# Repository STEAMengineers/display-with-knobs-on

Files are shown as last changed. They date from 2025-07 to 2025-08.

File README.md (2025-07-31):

# display-with-knobs-on

Think [cheap yellow display](https://github.com/witnessmenow/ESP32-Cheap-Yellow-Display) but not necessarily yellow and with two joystick inputs and four channels of brushed motor output. Originally designed to control [The open source underwater vehicle](https://github.com/concretedog/Tiny-Opensource-Underwater-Vehicle-TOUV-) project. 

## Features

* [RP2350b](https://datasheets.raspberrypi.com/rp2350/rp2350-product-brief.pdf) - Dual Arm Cortex-M33 or dual Hazard3 RISC-V processors
@ 150MHz
* [W25Q128JV-DTR](https://www.winbond.com/resource-files/w25q128jv_dtr%20revc%2003272018%20plus.pdf) - 16Mb primary flash 
* [MSP3520 screen](https://www.lcdwiki.com/3.5inch_SPI_Module_ILI9488_SKU%3AMSP3520) - ILI9488 powered 320x480 LCD screen with resistive touch and SD card slot (Headers)
* 2 x [TB6612FNG](https://toshiba.semicon-storage.com/us/product/linear/motordriver/detail.TB6612FNG.html) - Four channels of brushed motor outputs
* [IP5310](https://www.injoinic.com/api//static/uploads/20250528/20250528180445_6836dfbd54166.pdf) - Battery charger management with 3A boost output @ 5V for motors
* 2 x Joystick - Two axis analoge joysticks with push button inputs

  ## GPIO

  ### Motors

  A
  * IN1 - GPIO29
  * IN2 - GPIO28
  * PWM - GPIO24

  B
  * IN1 - GPIO31
  * IN2 - GPIO32
  * PWM - GPIO25

  STANDBY - GPIO30

  C
  * IN1 - GPIO34
  * IN2 - GPIO33
  * PWM - GPIO26

  D
  * IN1 - GPIO36
  * IN2 - GPIO37
  * PWM - GPIO27

  STANDBY - GPIO35

  ### Joysticks
  A
  * X - GPIO43
  * Y - GPIO44
  * Button - GPIO39
 
  B
  * X - GPIO41
  * Y - GPIO42
  * Button - GPIO38
 
  ### Screen

  Display
  * CS - GPIO13
  * RESET - GPIO18
  * DC/RS - GPIO17
  * MOSI - GPIO11
  * MISO - GPIO12
  * SCK - GPIO14
  * LED - GPIO16
 
  Touch
  * CS - GPIO10
  * IRQ - GPIO15
  * MOSI - GPIO11
  * MISO - GPIO12
  * SCK - GPIO14
 
  SD card
  * CS - GPIO21
  * SCK - GPIO22
  * MOSI - GPIO19
  * MISO - GPIO20

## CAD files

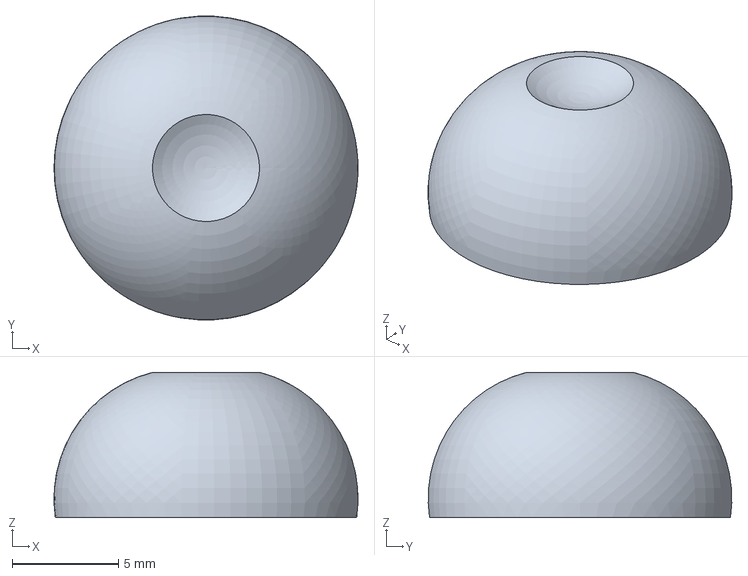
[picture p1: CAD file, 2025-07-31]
freecad/joystick_mushroom2.FCStd
14.3 x 14.3 x 6.82 mm

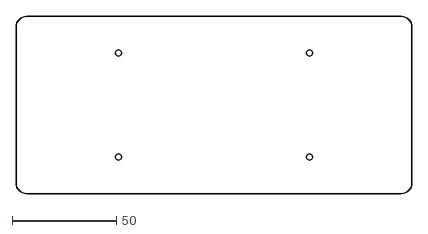
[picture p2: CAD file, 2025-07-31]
kicad/display-with-knobs-on/edgecuts.dxf
190.0 x 85.0

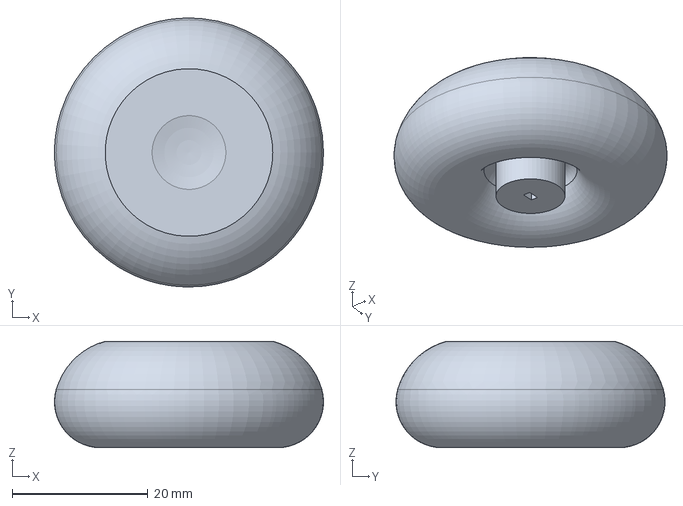
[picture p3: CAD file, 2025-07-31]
freecad/joystick_mushroom.FCStd
39.6 x 39.6 x 15.7 mm

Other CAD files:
freecad/joystick_mushroom.stl
freecad/joystick_mushroom2.stl

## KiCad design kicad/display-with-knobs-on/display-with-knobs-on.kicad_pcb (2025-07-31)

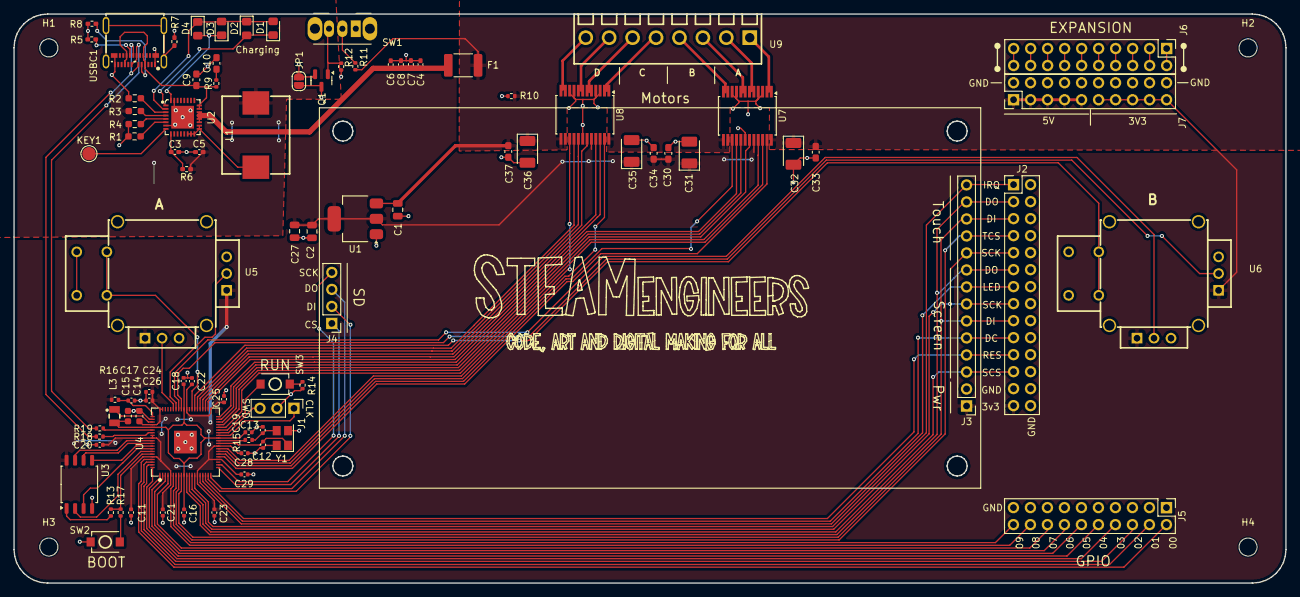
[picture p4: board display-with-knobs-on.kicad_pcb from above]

Board: 2 copper layers, 190.0 x 85.0 mm, 92 parts (1 on the bottom side), 106 nets.

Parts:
C1, C2, C27: 10u; C_0805_2012Metric
C3, C4, C5, C6, C7, C8: 22uF; C_0402_1005Metric_Pad0.74x0.62mm_HandSolder
C9, C10: 10uF; C_0603_1608Metric_Pad1.08x0.95mm_HandSolder
C11, C16, C19, C20, C21, C22, C23, C24, C25, C26, C28, C29: 100n; C_0402_1005Metric
C12, C13: 15p; C_0402_1005Metric
C14, C15: 4.7u; C_0603_1608Metric
C17, C18: 4.7u; C_0402_1005Metric
C30, C33, C34, C37: 0.1uF; C_0603_1608Metric_Pad1.08x0.95mm_HandSolder
C31, C32, C35, C36: 10uF; CP_EIA-3528-21_Kemet-B_Pad1.50x2.35mm_HandSolder
CN1: S2B-PH-SM4-TB(LF)(SN); CONN-SMD_P2.00_S2B-PH-SM4-TB-LF-SN
D1, D2, D3, D4: LED; LED_0805_2012Metric_Pad1.15x1.40mm_HandSolder
F1: Polyfuse; Fuse_1812_4532Metric_Pad1.30x3.40mm_HandSolder
H1, H2, H3, H4: MountingHole; MountingHole_2.7mm_M2.5
J1: Conn_01x03_Pin; PinHeader_1x03_P2.54mm_Vertical
J2: Conn_02x14_Odd_Even; PinHeader_2x14_P2.54mm_Vertical
J3: Conn_01x14_Socket; PinHeader_1x14_P2.54mm_Vertical
J4: Conn_01x04_Socket; PinHeader_1x04_P2.54mm_Vertical
J5, J6, J7: Conn_02x10_Odd_Even; PinHeader_2x10_P2.54mm_Vertical
JP1: Jumper_on; SolderJumper-2_P1.3mm_Open_RoundedPad1.0x1.5mm
KEY1: TestPoint; TestPoint_Pad_D2.0mm
L1: MHCC10040-1R0M-R7; IND-SMD_L11.6-W10.1
L3: 3.3u; IND-SMD_L2.0-W1.6_AOTA-B201610S3R3-101-T
Q1: JSM2302; SOT-23
R1: 51K; R_0603_1608Metric_Pad0.98x0.95mm_HandSolder
R2, R3, R4: 0; R_0603_1608Metric_Pad0.98x0.95mm_HandSolder
R5, R8: 5.1K; R_0402_1005Metric_Pad0.72x0.64mm_HandSolder
R6: 0; R_0402_1005Metric_Pad0.72x0.64mm_HandSolder
R7: 1M; R_0402_1005Metric_Pad0.72x0.64mm_HandSolder
R9: 2R; R_0402_1005Metric
R10: R120; R_0402_1005Metric
R11: 10K; R_0402_1005Metric
R12: 100K; R_0402_1005Metric
R13: 0; R_0402_1005Metric
R14, R15, R17: 1k; R_0402_1005Metric
R16: 33; R_0402_1005Metric
R18, R19: 27; R_0402_1005Metric
SW1: ON/OFF; SW_Slide_SPDT_Angled_CK_OS102011MA1Q
SW2, SW3: SW_Push; SW-SMD_L3.9-W3.0-P4.45
U1: NCP1117-3.3_SOT223; SOT-223-3_TabPin2
U2: IP5310; QFN-32_L5.0-W5.0-P0.50-BL-EP3.4
U3: W25Q128JVS; SOIC-8_5.23x5.23mm_P1.27mm
U4: RP2350_80QFN; QFN-80_L10.0-W10.0-P0.40-TL-EP3.4
U5, U6: YF16S-FL7.2-B5KB(45-10)-Y; JOYTICK-TH_YF16S-FL7.2-B5KB-45-10-Y_1
U7, U8: TB6612FNG; SSOP-24_5.3x8.2mm_P0.65mm
U9: DB125-3.5-8P-GN-S; CONN-TH_8P-P3.50_DORABO_DB125-3.5-8P-GN-S
USBC1: 105450-0101; USB-C-SMD_TYPE-C-USB-18
Y1: ABM8-272-T3; Crystal_SMD_3225-4Pin_3.2x2.5mm

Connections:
+1V1: C15.1, C16.1, C18.1, C19.1, L3.1, U4.10 (DVDD), U4.32 (DVDD), U4.51 (DVDD), U4.65 (VREG_FB)
+3V3: C2.1, C11.1, C14.1, C20.1, C21.1, C22.1, C23.1, C24.1, C25.1, C26.1, C27.1, C28.1, C29.1, C30.1, C31.1, C34.1, C35.1, J2.27, J3.1, J7.11, J7.13, J7.15, J7.17, J7.19, R16.1, U1.2 (VO), U3.8 (VCC), U4.5 (IOVDD), U4.15 (IOVDD), U4.24 (IOVDD), U4.29 (IOVDD), U4.41 (IOVDD), U4.50 (IOVDD), U4.59 (ADC_AVDD), U4.60 (IOVDD), U4.64 (VREG_VIN), U4.68 (USB_OTP_VDD), U4.69 (QSPI_IOVDD), U4.76 (IOVDD), U5.1, U5.4, U6.1, U6.4, U7.20 (VCC), U8.20 (VCC)
+5V: C1.1, C32.1, C33.1, C36.1, C37.1, F1.1, J7.1, J7.3, J7.5, J7.7, J7.9, R10.2, R11.1, U1.3 (VI), U7.13 (VM2), U7.14 (VM3), U7.24 (VM1), U8.13 (VM2), U8.14 (VM3), U8.24 (VM1)
+BATT: C5.1, CN1.2, L1.2, R3.1, R6.1
-BATT: C3.2, C4.2, C5.2, C6.2, C7.2, C8.2, C9.2, C10.2, CN1.1, JP1.1, Q1.2 (S), R1.1, R2.1, R4.1, R5.2, R7.2, R8.2, R12.2, U2.7 (AGND), U2.31 (LIGHT), U2.33 (EP), USBC1.A1 (GND), USBC1.A12 (GND), USBC1.B1 (GND), USBC1.B12 (GND)
/Controller/FLASH_SS: R13.2, U3.1 (~CS)
/Controller/QSPI_SCLK: U3.6 (CLK), U4.71 (QSPI_SCLK)
/Controller/QSPI_SD0: U3.5 (DI(IO0)), U4.72 (QSPI_SD0)
/Controller/QSPI_SD1: U3.2 (DO(IO1)), U4.74 (QSPI_SD1)
/Controller/QSPI_SD2: U3.3 (IO2), U4.73 (QSPI_SD2)
/Controller/QSPI_SD3: U3.7 (IO3), U4.70 (QSPI_SD3)
/Controller/QSPI_SS: R13.1, R17.1, U4.75 (QSPI_SS)
/Controller/RUN: SW3.2, U4.35 (RUN)
/Controller/VREG_AVDD: C17.1, R16.2, U4.61 (VREG_AVDD)
/Controller/VREG_LX: L3.2, U4.63 (VREG_LX)
/Controller/XIN: C12.1, U4.30 (XIN), Y1.1
/Controller/XOUT: R15.1, U4.31 (XOUT)
/Controller/~USB_BOOT: R17.2, SW2.2
/Power/VBUS: C9.1, R9.1, U2.23 (VIN), U2.24 (VIN), USBC1.A4 (VBUS), USBC1.A9 (VBUS), USBC1.B4 (VBUS), USBC1.B9 (VBUS)
A1: U7.1 (AO1), U7.2 (AO1), U9.1
A2: U7.5 (AO2), U7.6 (AO2), U9.2
ABUTTON: U4.48 (GPIO39), U5.8
AIN1: U4.37 (GPIO29), U7.21 (AIN1)
AIN2: U4.36 (GPIO28), U7.22 (AIN2)
AX: U4.54 (GPIO43_ADC3), U5.5
AY: U4.55 (GPIO44_ADC4), U5.2
B1: U7.11 (BO1), U7.12 (BO1), U9.4
B2: U7.7 (BO2), U7.8 (BO2), U9.3
BBUTTON: U4.47 (GPIO38), U6.8
BIN1: U4.39 (GPIO31), U7.17 (BIN1)
BIN2: U4.40 (GPIO32), U7.16 (BIN2)
BX: U4.52 (GPIO41_ADC1), U6.5
BY: U4.53 (GPIO42_ADC2), U6.2
C1: U8.1 (AO1), U8.2 (AO1), U9.5
C2: U8.5 (AO2), U8.6 (AO2), U9.6
CC1: R8.1, USBC1.A5 (CC1)
CC2: R5.1, USBC1.B5 (CC2)
CIN1: U4.43 (GPIO34), U8.21 (AIN1)
CIN2: U4.42 (GPIO33), U8.22 (AIN2)
D1: U8.11 (BO1), U8.12 (BO1), U9.8
D2: U8.7 (BO2), U8.8 (BO2), U9.7
D+: R18.1, USBC1.A6 (D+), USBC1.B6 (D+)
D-: R19.1, USBC1.A7 (D-), USBC1.B7 (D-)
DIN1: U4.45 (GPIO36), U8.17 (BIN1)
DIN2: U4.46 (GPIO37), U8.16 (BIN2)
GND: C1.2, C2.2, C11.2, C12.2, C13.2, C14.2, C15.2, C16.2, C17.2, C18.2, C19.2, C20.2, C21.2, C22.2, C23.2, C24.2, C25.2, C26.2, C27.2, C28.2, C29.2, C30.2, C31.2, C32.2, C33.2, C34.2, C35.2, C36.2, C37.2, J1.2, J2.2, J2.4, J2.6, J2.8, J2.10, J2.12, J2.14, J2.16, J2.18, J2.20, J2.22, J2.24, J2.25, J2.26, J2.28, J3.2, J5.1, J5.3, J5.5, J5.7, J5.9, J5.11, J5.13, J5.15, J5.17, J5.19, J7.2, J7.4, J7.6, J7.8, J7.10, J7.12, J7.14, J7.16, J7.18, J7.20, JP1.2, Q1.3 (D), R10.1, R14.2, SW2.1, U1.1 (GND), U3.4 (GND), U4.62 (VREG_PGND), U4.81 (GND), U5.3, U5.6, U5.7, U6.3, U6.6, U6.7, U7.3 (PGND1), U7.4 (PGND1), U7.9 (PGND2), U7.10 (PGND2), U7.18 (GND), U8.3 (PGND1), U8.4 (PGND1), U8.9 (PGND2), U8.10 (PGND2), U8.18 (GND), Y1.2, Y1.4
GPIO_0: J5.2, U4.77 (GPIO0)
GPIO_1: J5.4, U4.78 (GPIO1)
GPIO_2: J5.6, U4.79 (GPIO2)
GPIO_3: J5.8, U4.80 (GPIO3)
GPIO_4: J5.10, U4.1 (GPIO4)
GPIO_5: J5.12, U4.2 (GPIO5)
GPIO_6: J5.14, U4.3 (GPIO6)
GPIO_7: J5.16, U4.4 (GPIO7)
GPIO_8: J5.18, U4.6 (GPIO8)
GPIO_9: J5.20, U4.7 (GPIO9)
unnamed: C4.1, C6.1, C7.1, C8.1, F1.2, U2.19 (VOUT), U2.20 (VOUT), U2.21 (VOUT), U2.22 (VOUT)
unnamed: C10.1, R9.2
unnamed: C13.1, R15.2, Y1.3
unnamed: D1.2 (A), D2.1 (K), D3.2 (A), D4.1 (K), U2.2 (L3)
unnamed: D1.1 (K), D2.2 (A), U2.1 (L2)
unnamed: D3.1 (K), D4.2 (A), U2.32 (L1)
unnamed: J6.1, J6.2
unnamed: J6.3, J6.4
unnamed: J6.5, J6.6
unnamed: J6.7, J6.8
unnamed: J6.9, J6.10
unnamed: J6.11, J6.12
unnamed: J6.13, J6.14
unnamed: J6.15, J6.16
unnamed: J6.17, J6.18
unnamed: J6.19, J6.20
unnamed: L1.1, U2.14 (LX), U2.15 (LX), U2.16 (LX), U2.17 (LX), U2.18 (LX)
unnamed: Q1.1 (G), R12.1, SW1.3 (C)
unnamed: R14.1, SW3.1
unnamed: R11.2, SW1.2 (B)
unnamed: C3.1, R6.2, U2.9 (BAT)
unnamed: KEY1.1, U2.8 (KEY)
unnamed: R1.2, U2.6 (NTC)
unnamed: R4.2, U2.5 (RSET)
unnamed: R2.2, U2.3 (VSET)
unnamed: R3.2, U2.4 (VTHS)
unnamed: R19.2, U4.66 (USB_DM)
unnamed: R18.2, U4.67 (USB_DP)
unnamed: R7.1, USBC1.0
PWMA: U4.25 (GPIO24), U7.23 (PWMA)
PWMB: U4.26 (GPIO25), U7.15 (PWMB)
PWMC: U4.27 (GPIO26), U8.23 (PWMA)
PWMD: U4.28 (GPIO27), U8.15 (PWMB)
SC_CS: J2.23, J3.3, U4.12 (GPIO13)
SC_DC_RS: J2.19, J3.5, U4.17 (GPIO17)
SC_LED: J2.13, J3.8, U4.16 (GPIO16)
SC_RESET: J2.21, J3.4, U4.18 (GPIO18)
SC_SCK: J2.9, J2.15, J3.7, J3.10, U4.13 (GPIO14)
SC_SDI_MOSI: J2.5, J2.17, J3.6, J3.12, U4.9 (GPIO11)
SC_SDO_MISO: J2.3, J2.11, J3.9, J3.13, U4.11 (GPIO12)
SC_TS_CS: J2.7, J3.11, U4.8 (GPIO10)
SC_TS_IRQ: J2.1, J3.14, U4.14 (GPIO15)
SD_CS: J4.1, U4.21 (GPIO21)
SD_MISO: J4.3, U4.20 (GPIO20)
SD_MOSI: J4.2, U4.19 (GPIO19)
SD_SCK: J4.4, U4.22 (GPIO22)
STBY_A: U4.38 (GPIO30), U7.19 (STBY)
STBY_B: U4.44 (GPIO35), U8.19 (STBY)
SWCLK: J1.1, U4.33 (SWCLK)
SWD: J1.3, U4.34 (SWD)

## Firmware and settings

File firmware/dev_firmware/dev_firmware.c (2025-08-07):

#include <stdio.h>
#include "pico/stdlib.h"
#include "hardware/spi.h"
#include "hardware/adc.h"
#include "hardware/pwm.h"
#include "math.h"
#include "lib/screen.h"
#include "lvgl/lvgl.h"
#include "lib/anim_frames.h"
#include "motors.h"
#include "pins.h"

//#include "lib/ili9488.h"

//TODO -SCREEN

//Improve GUI
//  -Add image to controls
//  -Add animation picture frame


#define DISPLAY_WIDTH 480
#define DISPLAY_HEIGHT 320
// Buffer for the display
#define LV_COLOR_SIZE 2

static uint8_t buf1[DISPLAY_WIDTH * 320 * LV_COLOR_SIZE];


//float deadzone = 0.05f; // Deadzone for motor control
// Global variable to store the last speed of motor A
lv_obj_t * bar_motor_a = NULL;
// Global variable to store the last speed of motor B
lv_obj_t * bar_motor_b = NULL;

lv_obj_t *scale = NULL;
lv_obj_t *dial_label = NULL;
static lv_obj_t * dive_dial = NULL;

// Animation frames for the animation
const lv_image_dsc_t * anim_frames[] = {
    &animation00, &animation01, &animation02, &animation03, &animation04, &animation05, &animation06, &animation07,
    &animation08, &animation09, &animation10, &animation11, &animation12, &animation13, &animation14, &animation15,
    &animation16, &animation17, &animation18, &animation19, &animation20, &animation21, &animation22, &animation23,
    &animation24, &animation25, &animation26, &animation27, &animation28, &animation29, &animation30, &animation31,
    &animation32, &animation33, &animation34, &animation35, &animation36, &animation37
};

const uint8_t anim_frame_count = sizeof(anim_frames) / sizeof(anim_frames[0]);
static lv_obj_t * anim_img = NULL;
static uint8_t anim_frame_idx = 0;

static void anim_img_timer_cb(lv_timer_t * timer) {
    anim_frame_idx = (anim_frame_idx + 1) % anim_frame_count;
    lv_image_set_src(anim_img, anim_frames[anim_frame_idx]);
}

static uint32_t my_tick(void) {

	return to_ms_since_boot(get_absolute_time());
}

void lv_dashboard_set(void)
{
    // Main container (screen)
    lv_obj_t * cont = lv_obj_create(lv_screen_active());
    lv_obj_set_size(cont, 480, 320);
    lv_obj_center(cont);
    lv_obj_set_style_pad_all(cont, 0, 0);
    lv_obj_set_style_border_width(cont, 0, 0);
    lv_obj_set_scrollbar_mode(cont, LV_SCROLLBAR_MODE_OFF);
    lv_obj_set_style_bg_img_src(cont, &display_background, 0);

    // Add left label
    lv_obj_t * img1 = lv_image_create(cont);
    lv_image_set_src(img1, &left);
    lv_obj_set_pos(img1, 50, 40);

    // Create a vertical bar in col1
    bar_motor_a = lv_slider_create(cont);
    lv_obj_set_size(bar_motor_a, 20, 180); // width, height
    lv_obj_set_style_pad_bottom(bar_motor_a, 30, 0);
    lv_obj_set_pos(bar_motor_a, 80, 80);
    lv_slider_set_range(bar_motor_a, -4095, 4095); // -100% to +100%
    lv_slider_set_value(bar_motor_a, 0, LV_ANIM_OFF); // Start at 0

    static lv_style_t style_main;
    static lv_style_t knob_style;
    static lv_style_t style_indicator;

    lv_style_init(&style_main);
    lv_style_set_bg_color(&style_main, lv_color_hex(0x000000));
    lv_style_set_bg_opa(&style_main, LV_OPA_COVER);
    lv_style_set_border_width(&style_main, 0);
    lv_style_set_radius(&style_main, 2);
    lv_style_set_width(&style_main, 10); // Set bar width
    lv_style_set_shadow_width(&style_main, 2);
    lv_obj_add_style(bar_motor_a, &style_main, LV_PART_MAIN);
 
    lv_style_init(&knob_style);
    lv_style_set_pad_top(&knob_style, -25); //Makes no sense but it works
    lv_style_set_width(&knob_style, 50);  // Set knob width
    lv_style_set_height(&knob_style, 42); // Set knob height
    lv_style_set_bg_opa(&knob_style, 0);
    lv_style_set_bg_image_src(&knob_style, &slot_knob_small);
    lv_obj_add_style(bar_motor_a, &knob_style, LV_PART_KNOB);

    //Hide indicator
    lv_obj_set_style_opa(bar_motor_a, LV_OPA_TRANSP, LV_PART_INDICATOR);
    
    // Add a label to col2
    lv_obj_t * img2 = lv_image_create(cont);
    lv_image_set_src(img2, &right);
    lv_obj_set_pos(img2, 160, 40);

    // Create a vertical bar in col2
    bar_motor_b = lv_slider_create(cont);
    lv_obj_set_size(bar_motor_b, 20, 180); 
    lv_obj_set_style_pad_bottom(bar_motor_b, 30, 0);
    lv_obj_set_pos(bar_motor_b, 195, 80);
    lv_bar_set_range(bar_motor_b, -4095, 4095); // -100% to +100%
    lv_slider_set_value(bar_motor_b, 0, LV_ANIM_OFF); // Start at 0
    lv_obj_add_style(bar_motor_b, &style_main, LV_PART_MAIN);
    lv_obj_add_style(bar_motor_b, &knob_style, LV_PART_KNOB);
    //Hide indicator
    lv_obj_set_style_opa(bar_motor_b, LV_OPA_TRANSP, LV_PART_INDICATOR);
  
    // Add a label to col3


    lv_obj_t * img3 = lv_image_create(cont);
    lv_image_set_src(img3, &dive);
    lv_obj_set_pos(img3, 335, 38);

    // Add a dial to col3_row2 to show dive motor speed
    dive_dial = lv_arc_create(cont);
    lv_obj_set_size(dive_dial, 110, 110);
    lv_obj_set_pos(dive_dial, 318, 80);

    // Set range and sweep
    lv_arc_set_range(dive_dial, -100, 100);
    lv_arc_set_mode(dive_dial, LV_ARC_MODE_NORMAL); // 180° sweep
    lv_arc_set_rotation(dive_dial, 180);            // Start at bottom
    lv_arc_set_bg_angles(dive_dial, 0, 180);      // Background arc from 0° to 180°

    static lv_style_t style_dive_main;
    static lv_style_t knob_dive_style;

    lv_style_init(&style_dive_main);
    lv_style_set_arc_color(&style_dive_main, lv_color_hex(0x000000));
    lv_obj_add_style(dive_dial, &style_dive_main, LV_PART_MAIN);

    lv_style_init(&knob_dive_style);
    lv_style_set_bg_color(&knob_dive_style, lv_color_hex(0xBB0000));
    lv_obj_add_style(dive_dial, &knob_dive_style, LV_PART_KNOB);

    //Hide indicator
    lv_obj_set_style_opa(dive_dial, LV_OPA_TRANSP, LV_PART_INDICATOR);

    // Add a label below the dial
    dial_label = lv_label_create(cont);
    lv_obj_set_pos(dial_label, 363, 120); 
    lv_label_set_text(dial_label, LV_SYMBOL_MINUS);
    lv_obj_set_style_text_font(dial_label, &lv_font_montserrat_24, 0);

    //Animation image in col3_row3
    anim_img = lv_image_create(cont);
    lv_image_set_src(anim_img, anim_frames[0]);
    //lv_obj_set_align(anim_img, LV_ALIGN_TOP_MID);
    lv_obj_set_pos(anim_img, 300, 170);   
    lv_timer_create(anim_img_timer_cb, 100, NULL); // 100 ms interval for animation

}

int main()
{
    stdio_init_all();
    printf("Booting...\n");
    printf("Pico SDK Version: %s\n", PICO_SDK_VERSION_STRING);
    printf("========================================\n");
    printf("Display with Knobs on Firmware\n");
    printf("========================================\n");

    printf("Initialising GPIOs...\n");
    adc_init();
    adc_gpio_init(41);
    adc_gpio_init(42);
    adc_gpio_init(43);
    adc_gpio_init(44);

    printf("Initialising motors...\n");
    initialise_motors();
    
    printf("Initialising LVGL...\n");
    // Initialise LVGL
    lv_init();
    lv_tick_set_cb(my_tick);
    screen_init();
    screen_clear(0xf800);
    lv_display_t * display1 = lv_display_create(DISPLAY_WIDTH, DISPLAY_HEIGHT);
    if (display1 == NULL) {
        printf("Failed to create display\n");
        return -1;
    }
    lv_display_set_buffers(display1, buf1, NULL, sizeof(buf1), LV_DISPLAY_RENDER_MODE_PARTIAL);
    lv_display_set_flush_cb(display1, my_flush_cb); 
    lv_obj_set_style_bg_color(lv_screen_active(), lv_color_hex(0x888888), 0);
    lv_obj_invalidate(lv_screen_active());
    lv_dashboard_set();

    while (1) {
        adc_select_input(4);  //Joystick A x
        uint adc_x_raw = adc_read();
        adc_select_input(3);  //Joystick A y
        uint adc_y_raw = adc_read();
        adc_select_input(1);  //Joystick B y
        uint adc_z_raw = adc_read();

        //printf("X: %d, Y: %d, Z: %d\n", adc_x_raw, adc_y_raw, adc_z_raw);
        float adc_x_norm = (((float)adc_x_raw -2105)/2105) * -1.0f; // Normalize to -1.0 to 1.0
        float adc_y_norm = (((float)adc_y_raw -2105)/2105) * -1.0f; // Normalize to -1.0 to 1.0

        float left, right;
        differential_drive(adc_x_norm, adc_y_norm, deadzone, &left, &right); // 0.05f deadzone

        motor_set_speed(MOTOR_A_PWM_PIN, MOTOR_A_IN1_PIN, MOTOR_A_IN2_PIN, left);
        motor_set_speed(MOTOR_B_PWM_PIN, MOTOR_B_IN1_PIN, MOTOR_B_IN2_PIN, right);

        lv_bar_set_value(bar_motor_a, (int)(last_motor_a_speed * 4095), LV_ANIM_OFF);
        lv_bar_set_value(bar_motor_b, (int)(last_motor_b_speed * 4095), LV_ANIM_OFF);

        // Normalize adc_z_raw to -1.0 .. 1.0 (centered at 2105)
        float adc_z_norm = (((float)adc_z_raw - 2105) / 2105.0f) * -1.0f;
        if (adc_z_norm > 1.0f) adc_z_norm = 1.0f;
        if (adc_z_norm < -1.0f) adc_z_norm = -1.0f;

        dive_motor_drive(adc_z_norm, deadzone); // 0.05f deadzone
        
        // Calculate the angle for the needle based on scale_value (-100 to 100 mapped to 135 to 405 degrees)
        int scale_value;
        if(fabsf(adc_z_norm) < deadzone) {
            scale_value = 0;
        } else {
            scale_value = (int)roundf(adc_z_norm * 100.0f);
        }
        // Update the arc dial value
        lv_arc_set_value(dive_dial, scale_value);
if (fabsf(adc_z_norm) < deadzone) {
    lv_label_set_text(dial_label, LV_SYMBOL_MINUS);
} else if (scale_value > 0) {
    lv_label_set_text(dial_label, LV_SYMBOL_UP);
} else if (scale_value < 0) {
    lv_label_set_text(dial_label, LV_SYMBOL_DOWN);
} else {
    lv_label_set_text(dial_label, "-");
}


        lv_timer_handler(); // Call the LVGL timer handler to process events
        sleep_ms(100); // Sleep for a short time to allow LVGL to process events


    }
    return 0;
}

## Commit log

2025-07-31 Add joystick key design for TPU
    [joystick_mushroom.FCStd, joystick_mushroom.stl, joystick_mushroom2.FCStd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]
2025-07-31 Initial hardware commit
    [TOUV_controller.kicad_sch, TOUV_power.kicad_sch, battery.kicad_sch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]
2025-08-05 Refactor motor functions, fix differential drive
    [dev_firmware.c]
2025-08-07 Update uf2 to current build
